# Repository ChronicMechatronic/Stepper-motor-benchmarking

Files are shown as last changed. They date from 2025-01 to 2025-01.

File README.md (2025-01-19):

# Stepper-motor-benchmarking
Collection of all test results and data from thoroughly testing my collection of random stepper motors

This repository contains all results and data from extensively testing the microstepping capabilities as well as any specifications I found online for each of the following stepper motors:

 - USONGSHINE US-17HS4401S
 - EPSON EM-257 / EM-258
 - JAPAN SERVO KP39HM2-025
 - EM-164 / STH-39D179-03 (unknown manufacturer)
 - MOONS 17HA0403-75NS
 - MOONS 16HY7401-44S
 - JAPAN SERVO KP35FM2-044
 - LIN ENGINEERING 3518M-10D-01RO
 - MERCURY MOTOR SM-42BYG011-25
 - 42HJA440-23 (unknown manufacturer)
 - TRONXY 42SHDC4080Z-25B
 - KYSAN 1124090 / 42BYGH4803-DC
 - HANPOSE 17HS4401
 - WANTAI MOTOR 42BYGHW609-1

For information about my test procedure and how to interpret the data, watch the [full video](https://www.youtube.com/watch?v=Vqqj7FCdkGw) on my YouTube channel

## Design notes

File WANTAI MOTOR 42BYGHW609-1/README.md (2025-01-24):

## WANTAI MOTOR 42BYGHW609-1 

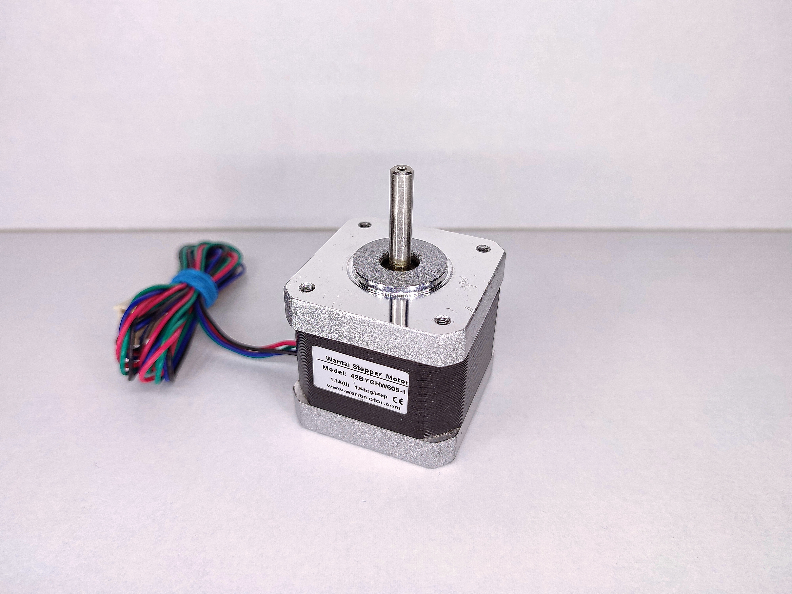
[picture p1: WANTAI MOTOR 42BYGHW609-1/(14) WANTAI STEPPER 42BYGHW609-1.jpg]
image of a stepper motor


It's a stepper motor aimed at the 3D printing industry. That's all there is to say about it. Low phase resistance, low inductance, high current - it's all pretty standard stuff. The WANTAI MOTOR website lists the specs:

 - https://www.wantmotor.com/hybrid-stepper-motor/2-phases-hybrid-stepper-motor/42byghw-stepper-motor.html
 - Open Impulse seems to have put together a datasheet for it with even a torque curve added, though at the time of writing this the site didn't manage to load for some reason: https://www.openimpulse.com/blog/wp-content/uploads/wpsc/downloadables/42BYGHW609-Stepper-Motor-Datasheet1.pdf

Good news, however, to prepare for exactly that eventuality (a site being taken down or otherwise unavailable), I added the downloaded PDFs to this repository. You're welcome!

Of course, the usual disclaimer still applies; intellectual property rights for any graphics and logos depicted in screenshots of those sites obviously go to their respective site owners and are not part of this open-source repository, as I have no rights to distribute these myself. (in other words, stating the obvious to make sure I cover my ass for legal purposes here: the fact that I'm sharing screenshots with these logos and graphics in them in a CC-BY-SA-4.0 repository doesn't mean the license extends to those graphics)

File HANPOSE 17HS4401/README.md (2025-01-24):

## HANPOSE 17HS4401

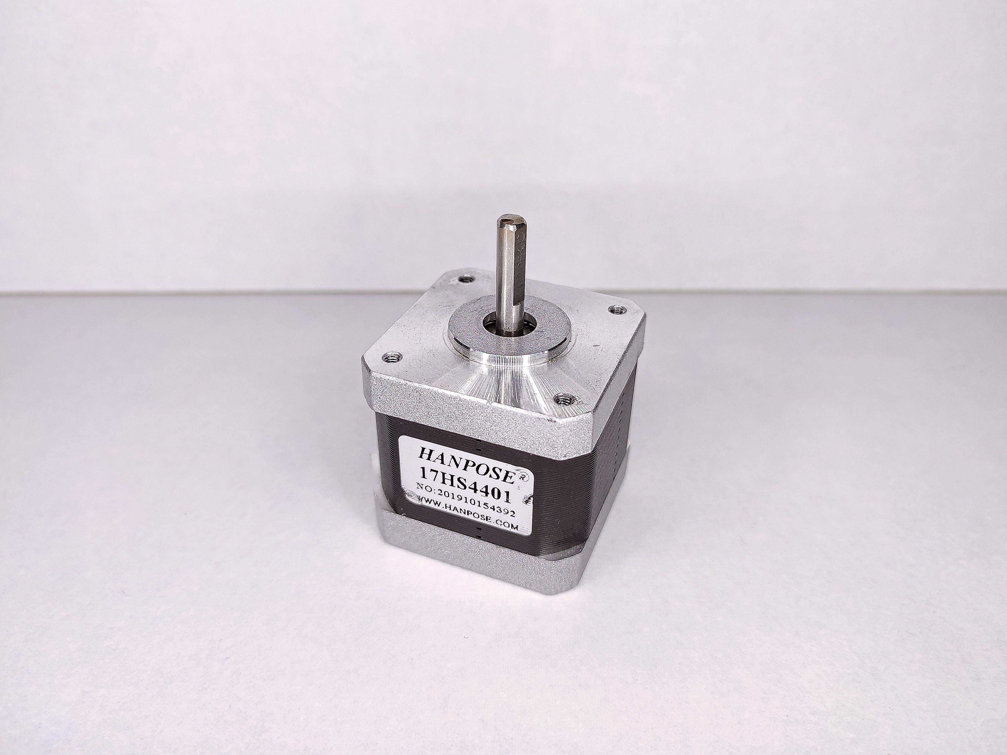
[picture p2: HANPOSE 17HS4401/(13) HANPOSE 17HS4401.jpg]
image of a stepper motor


In my opinion, companies should really stop making products with different specs under the same model number, but oh well... This is the 17HS4401 model from HANPOSE, which, compared to the USONGSHINE version, has a marginally lower holding torque at the same current - which I guess makes sense considering it also has a lower phase resistance and thereby fewer turns per coil. On the other hand, this should mean lower inductance and higher maximum speeds... I'm speculating at this point; I really wanted to see the exact differences between these two models in the dynamic torque tests, but I guess that'll have to wait for another day. In any case, there weren't any datasheets available for this motor, but the Alibaba product page lists current and holding torque at least:

 - https://www.alibaba.com/product-detail/HANPOSE-Direct-purchase-price-40N-CM_62405772411.html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

There's also an exported PDF version as a backup in case the site goes down in the future.

Intellectual property rights for any graphics and logos depicted in screenshots of websites obviously go to their respective site owners and are not part of this open-source repository.

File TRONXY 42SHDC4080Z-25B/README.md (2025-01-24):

## TRONXY 42SHDC4080Z-25B

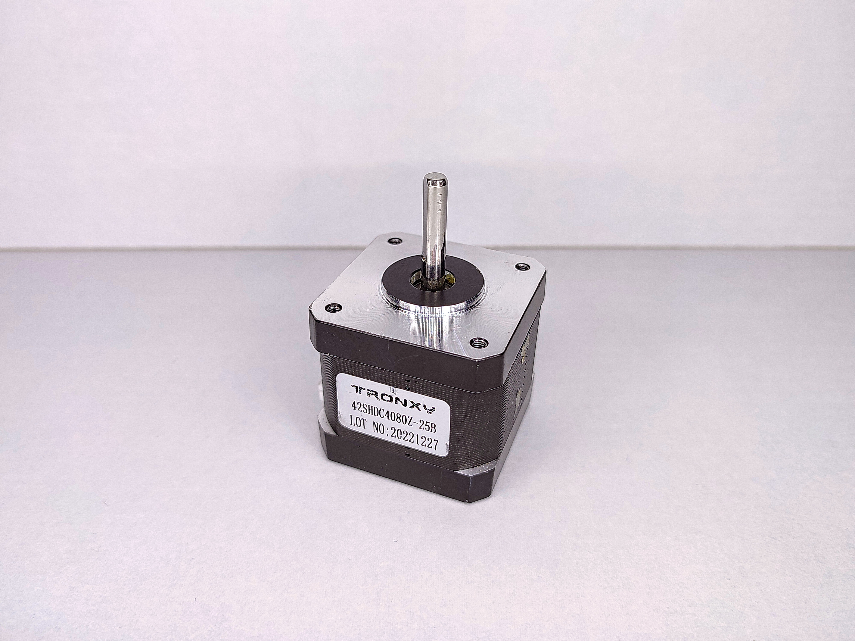
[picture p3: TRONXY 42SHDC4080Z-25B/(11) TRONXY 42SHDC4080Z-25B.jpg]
image of a stepper motor


This stepper motor is clearly from a TRONXY 3D printer, which is why I was all the more surprised by the fact that there was absolutely no info about it online. Ultimately I guess it's just another generic clone of an obscure Chinese stepper motor. Unfortunately, Tronxy also didn't bother to list any specs anywhere either, as the replacement steppers they sell on their website have a different part number altogether. They're called "SL42STH40" instead, so short of sending TRONXY an email asking about the specs (which I don't feel bold enough to do), we're basically on our own if we want specs for the 42SHDC... Or are we? With a bit of _imaginative_ reasoning, we can assume the SL42STH40 steppers they currently sell are very similar clones - after all, what are the odds they actually changed suppliers or specifications? Relatively low, is my gut feeling. Physically they look identical save for the label, which obviously doesn't say much. So since I needed a baseline current rating for my testing, I decided to just go with the same 1.8A current rating they claim for their current SL42STH motor. Though I'm honestly not sure whether to trust that rating either, despite the low 1.6Ω winding resistance suggesting this motor would indeed run at a higher current than its 3Ω NEMA 17 brethren. So in continuous use, I would probably run this motor closer to 1.5A or less, depending on how hot it gets. If you happen to have one of these, please run your own tests; even something simple with an A4988 like I did in the video will easily give you a much more reliable reference and prevent anything from being damaged. I just didn't have the time to spend another day letting stepper motors run idle in the basement.

That said, here are the few most relevant-looking search results I was able to come up with:

 - https://www.tronxy3d.com/collections/motor/products/sl42sth40-1684a-1-8a-78oz-in-42-stepper-motor
 - https://botland.store/flashforge-replacement-parts/18649-stepper-motor-42shdc1065z-19wt-200-steps-448v-08a-028nm-for-flashforge-adventurer-3-5904422362294.html
 - https://www.tronxy3d.com/products/tronxy-3d-printer-parts-sl42sth60-1684a-motor-with-1-5m-cable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
 - https://www.alibaba.com/product-detail/42SHDC3025-24B-stepper-motor-for-eco_1600961608090.html
 - https://french.alibaba.com/product-detail/CE-Approved-2-Phase-Stepper-1-62149025114.html

There are also exported PDF versions for some of these sites as a backup in case any of them goes down in the future.

Intellectual property rights for any graphics and logos depicted in screenshots of those sites obviously go to their respective site owners and are not part of this open-source repository, as I have no rights to distribute these myself. (in other words, stating the obvious to make sure I cover my ass for legal purposes here: the fact that I'm sharing screenshots with these logos and graphics in them in a CC-BY-SA-4.0 repository doesn't mean the license extends to those graphics)

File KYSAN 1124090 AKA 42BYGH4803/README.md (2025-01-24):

## KYSAN 1124090 / 42BYGH4803

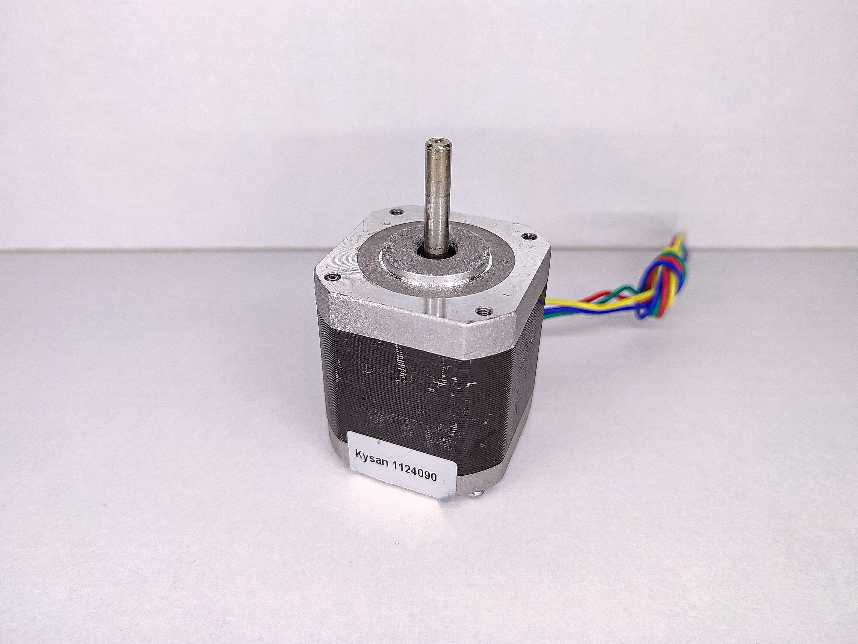
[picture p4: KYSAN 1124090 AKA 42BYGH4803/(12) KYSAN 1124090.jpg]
image of a stepper motor


Apparently this 42BYGH4803 stepper motor was rather common in RepRap 3D printers back in the day. It's from KYSAN with the SKU 1124090, and I really can't think of anything else to say about it. It's a stepper motor, I guess.

Here are the relevant links to product pages listing the specs and datasheets:

 - https://kysanelectronics-com.3dcartstores.com/42BYGH4803-DC_p_672.html
 - https://www.kysanelectronics.com/graphics/1124090-8.3.15.pdf
 - https://ultimachine.com/products/kysan-1124090-nema-17-stepper-motor
 - https://cdn.shopify.com/s/files/1/1223/5992/files/1124090_Torque_curve_diagram.pdf?6848101445132525963
 - https://cdn.shopify.com/s/files/1/1223/5992/files/Nema17StepperMotor.pdf?6848101445132525963

There are also PDF versions of the datasheets as a backup in case any of the websites go down in the future.

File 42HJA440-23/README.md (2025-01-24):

## 42HJA440-23 (unknown manufacturer)

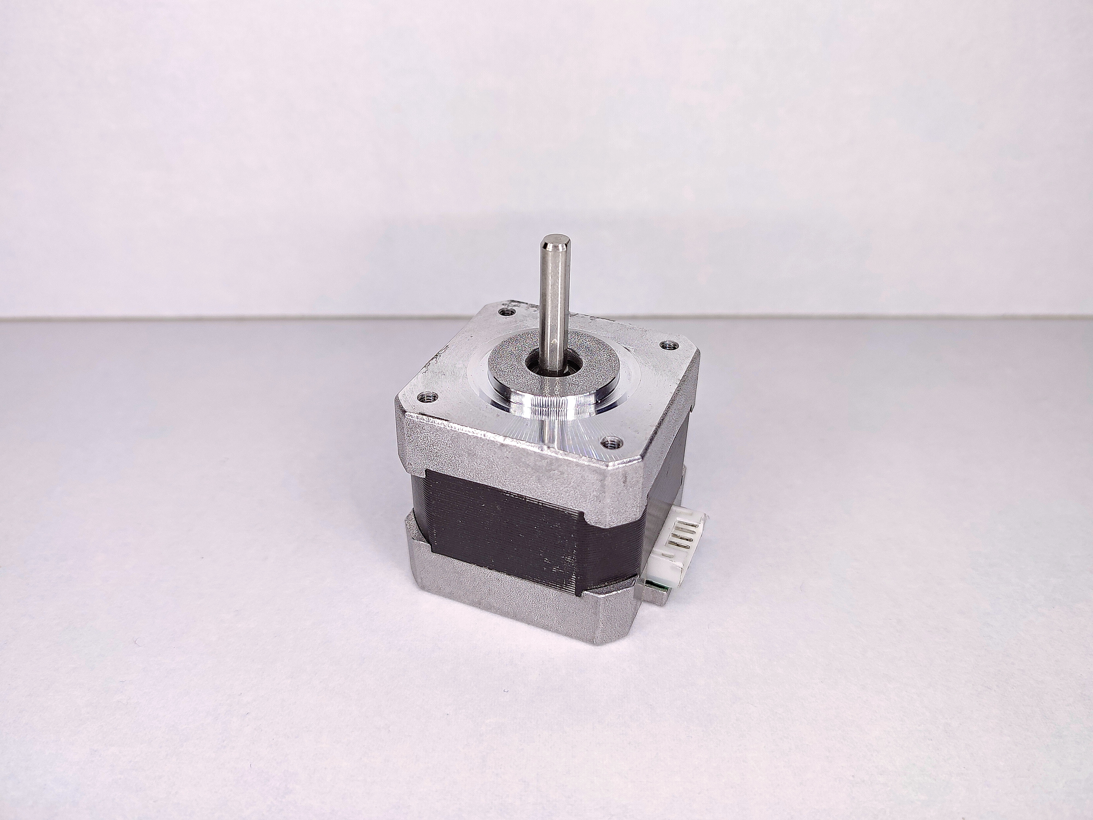
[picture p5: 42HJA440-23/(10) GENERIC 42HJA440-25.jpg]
image of a stepper motor


This stepper motor is a total mystery - it looks about as generic as things can get, and the total lack of identifying features other than the part number stamped on the back makes it all the more intriguing to me. But probably it's just another clone of a clone. I'll certainly work fine for a 3D printer or something, with a microstepping performance on par with that of most other modern Chinese low-cost steppers. Since I didn't find a concrete current rating, I theoretically should've established a new one through actual testing, but seeing as these NEMA 17s are all so similar, I basically just guesstimated a value that felt right. Taking the relatively low phase resistance of only 1.5Ω into account, I went with 1.64A, which is definitely as arbitrary as it is to be taken with a grain of salt. In continuous use, I would probably run this motor closer to 1.5A or less, depending on how hot it gets. If you happen to have one of these, please run your own tests; even something simple with an A4988 like I did in the video will easily give you a much more reliable reference and prevent anything from being damaged. That said, I needed a baseline for my testing and couldn't spend another day letting stepper motors run idle in the basement.

Here some of the search results that sounded the most relevant, though none of them is actually referring to this model as far as I can tell:

 - https://www.made-in-china.com/showroom/seaweedtan/product-detailzMAEstGCaZRr/China-42mm-Stepper-Motor-for-Lighting-Equipment-42HJA440-20-.html
 - https://www.ubuy.fr/en/catalog/product/view/id/12983460/s/dp-cinkco-nema-17-stepper-motor-2phase-17-bipolar
 - https://www.machineto.com/textile-printing-equipment-stepper-motor-10238961

There are also exported PDF versions for each of these sites as a backup in case any of them goes down in the future.

Intellectual property rights for any graphics and logos depicted in screenshots of those sites obviously go to their respective site owners and are not part of this open-source repository, as I have no rights to distribute these myself. (in other words, stating the obvious to make sure I cover my ass for legal purposes here: the fact that I'm sharing screenshots with these logos and graphics in them in a CC-BY-SA-4.0 repository doesn't mean the license extends to those graphics)

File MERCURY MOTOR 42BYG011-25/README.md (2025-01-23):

## MERCURY MOTOR 42BYG011-25

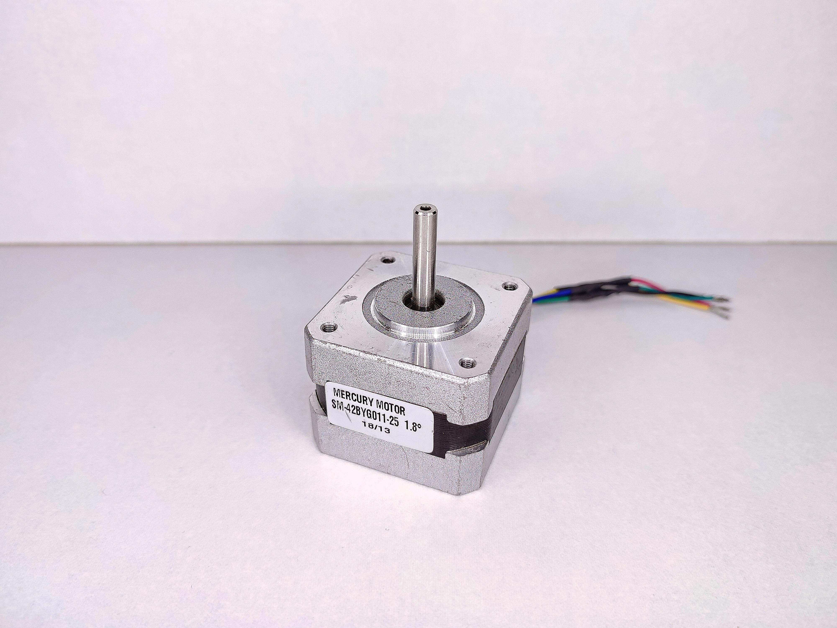
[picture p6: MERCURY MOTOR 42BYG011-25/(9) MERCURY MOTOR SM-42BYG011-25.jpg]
image of a stepper motor


This stepper is from Sparkfun and readily available on DigiKey - it also has a very high phase resistance of 34 ohms, which is definitely unusual. I don't know why bipolar motors with this winding configuration are even still manufactured, seeing as the general push has been towards low-resistance, actively current-controlled motors for years now, but I guess there are a few niche applications where having the current regulated passively by good old Ohm's law prevails over modern alternatives by enabling a simple H-bridge drive circuitry to be used.

 - Here the product page on DigiKey: https://www.digikey.com/en/products/detail/sparkfun-electronics/ROB-09238/5318747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
 - And the datasheet, of course: https://www.sparkfun.com/datasheets/Robotics/SM-42BYG011-25.pdf

There are also exported PDF versions for each of these sites as a backup in case any of them goes down in the future.

Intellectual property rights for any graphics and logos depicted in screenshots of those sites obviously go to their respective site owners and are not part of this open-source repository, as I have no rights to distribute these myself. (in other words, stating the obvious to make sure I cover my ass for legal purposes here: the fact that I'm sharing screenshots with these logos and graphics in them in a CC-BY-SA-4.0 repository doesn't mean the license extends to those graphics)

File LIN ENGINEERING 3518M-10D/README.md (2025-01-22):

## LIN ENGINEERING 3518M-10D

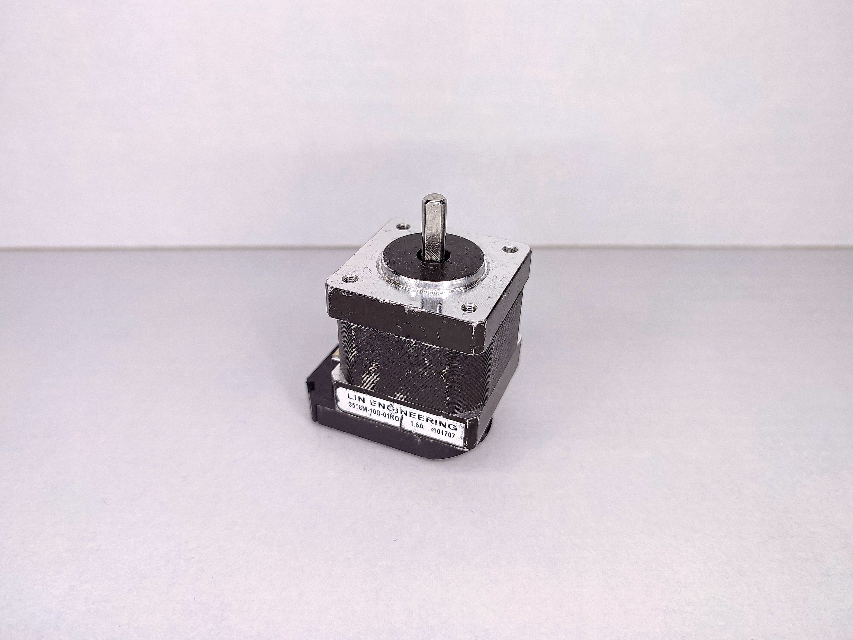
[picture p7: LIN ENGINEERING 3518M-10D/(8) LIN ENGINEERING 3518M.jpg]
image of a stepper motor


While LIN ENGINEERING (being a subsidiary of MOONS) generally provides good documentation for their stepper motors, this one sure seems like a customized version of one of their models - the coil parameters of this one don't match up at all with the ones they list on their website for the 3518M - it has a phase resistance of only about 1.0 ohm, which doesn't fit in with any of their other model series either as far as I could tell. Fortunately, the current rating is printed right on the label, so the lack of other specifications didn't impede my testing.

 - Here's a link to their 3518M series, though I wouldn't rely on any of the electrical specifications: https://www.linengineering.com/products/stepper-motors/hybrid-stepper-motors/3518-series/3518M-07

 - And another NEMA 14 of theirs with a similar current rating that I at first thought they might've taken the coil configuration from, but it still has twice the phase resistance of mine... https://www.linengineering.com/products/stepper-motors/hybrid-stepper-motors/3518-series/3518L-15P

There are also exported PDF versions of these sites as a backup in case any of them goes down in the future.

Intellectual property rights for any graphics and logos depicted in screenshots of those sites obviously go to their respective site owners and are not part of this open-source repository, as I have no rights to distribute these myself. (in other words, stating the obvious to make sure I cover my ass for legal purposes here: the fact that I'm sharing screenshots with these logos and graphics in them in a CC-BY-SA-4.0 repository doesn't mean the license extends to those graphics)

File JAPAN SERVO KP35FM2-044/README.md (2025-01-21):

## JAPAN SERVO KP35FM2-044

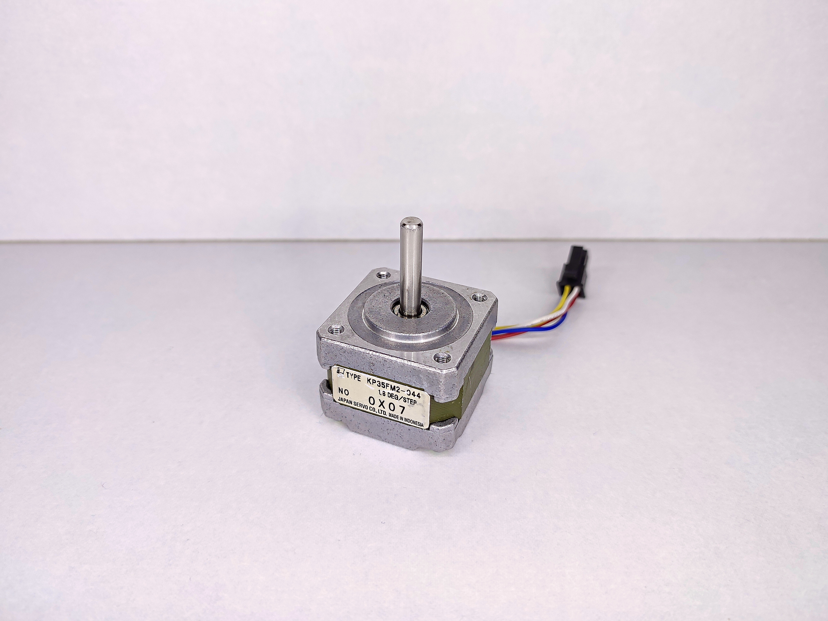
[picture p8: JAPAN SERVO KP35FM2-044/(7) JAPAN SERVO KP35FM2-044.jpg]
image of a stepper motor


Another stepper motor from JAPAN SERVO - though this one is fortunately bipolar and quite usable in its stock configuration. I was actually able to find two references to this exact model online.

 - A product page for it on some (Serbian?) website: https://www.interhit.rs/razno/12919-mot-kp35fm2-044-2000000137841.html
 - A page of some mail-order-catalog listing the important specs: https://www.jameco.com/Jameco/catalogs/c111/P113.pdf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

No real datasheets, though unfortunately. I also included exported PDF versions for each of these sites as a backup in case any of them goes down in the future.

Intellectual property rights for any graphics and logos depicted in screenshots of those sites obviously go to their respective site owners and are not part of this open-source repository, as I have no rights to distribute these myself. (in other words, stating the obvious to make sure I cover my ass for legal purposes here: the fact that I'm sharing screenshots with these logos and graphics in them in a CC-BY-SA-4.0 repository doesn't mean the license extends to those graphics)

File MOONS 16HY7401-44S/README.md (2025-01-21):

## MOONS 16HY7401-44S

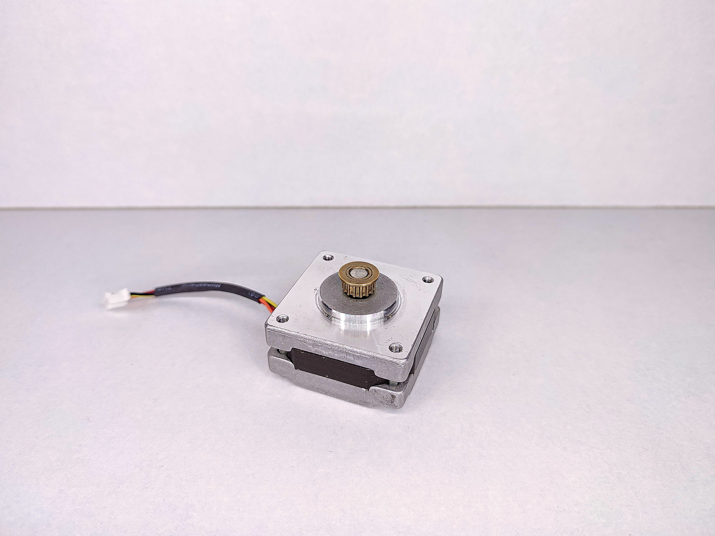
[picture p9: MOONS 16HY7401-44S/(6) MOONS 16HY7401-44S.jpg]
image of a stepper motor


Yet another pancake stepper from MOONS with an annoying brass pulley on it - finding even a picture of a matching unit was impossible, but I managed to find some specs on an ancient derelict website:

 - http://www.huaning.com/oldwebsite/electrical/16hy.htm

Not sure if this is specifically for the MOONS edition of this motor or maybe some other manufacturer's version of it (since I noticed, just like with semiconductors, the more popular models seem to be made by several different companies with very slightly different specs), though seeing as I wasn't able to find anything else whatsoever, it's safe to assume these are the right specs for the stepper.

There's also an exported PDF version of this site as a backup in case somebody remembers to decommission that forgotten-about server in the corner and takes the site down in the future.

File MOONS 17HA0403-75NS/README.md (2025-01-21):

## MOONS 17HA0403-75NS

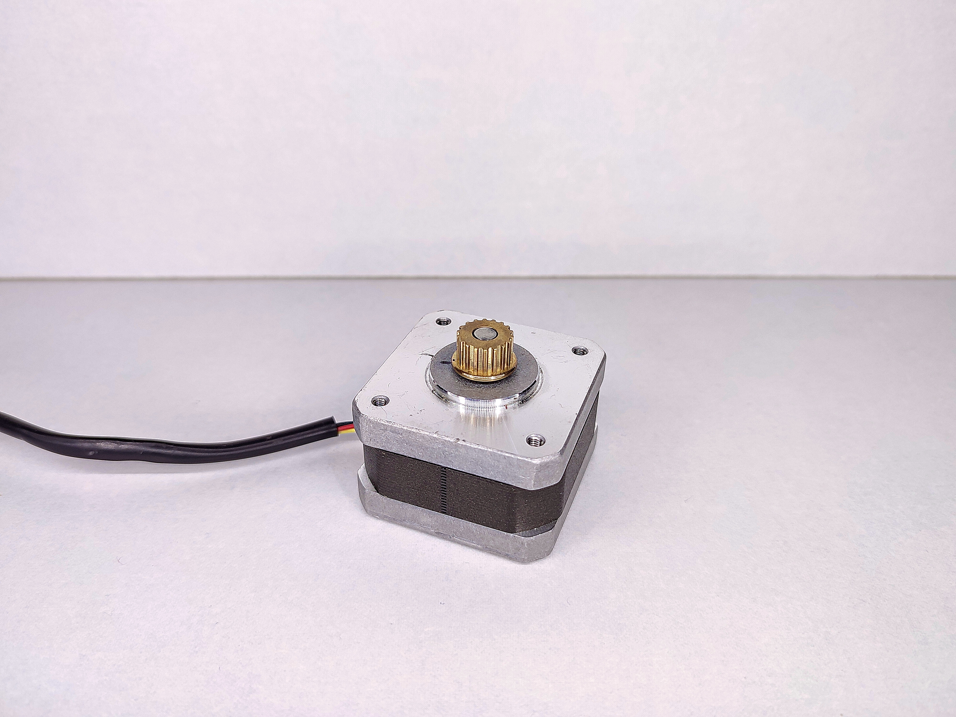
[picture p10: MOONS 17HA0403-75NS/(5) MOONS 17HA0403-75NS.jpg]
image of a stepper motor


I really can't say what device this stepper motor is from - the brass pulley on it is not GT2 size though, so for most DIY projects you'll probably have to remove it, which is more than a little annoying. I recommend a hacksaw to destroy the pulley as the easiest way to get it off - I wanted to keep the motor and the pulley intact, so I had to machine a custom gear puller that actually fit in the tight gap between the motor housing and the pulley flange.

Fortunately, I was able to find what I am relatively confident is the datasheet for this motor - there's even two versions of it:

- https://datasheet4u.com/datasheet-pdf/ETC/17HA0403-44N/pdf.php?id=977470
- http://www.motionusa.com.s3-website-us-east-1.amazonaws.com/moons/Hybrid_Stepper_Motors_17HA_Series.pdf

There's also a very similar looking one with a 1.8 step angle instead, though I think it might not be from MOONS - No idea what you might need this for, but here's the link anyway:
 - https://www.sinoning.com/product/17ha0403-17n-micro-precision-stepper-motor-42mm-1-8-degree-2-phase-4-wire-stepping-motor-pulley-cnc-3d-printer-diy/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

There are also exported PDF versions for each of these sites as a backup in case any of them goes down in the future.

Intellectual property rights for any graphics and logos depicted in screenshots of those sites obviously go to their respective site owners and are not part of this open-source repository, as I have no rights to distribute these myself. (in other words, stating the obvious to make sure I cover my ass for legal purposes here: the fact that I'm sharing screenshots with these logos and graphics in them in a CC-BY-SA-4.0 repository doesn't mean the license extends to those graphics)

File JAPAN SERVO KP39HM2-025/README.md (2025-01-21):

## JAPAN SERVO KP39HM2-025

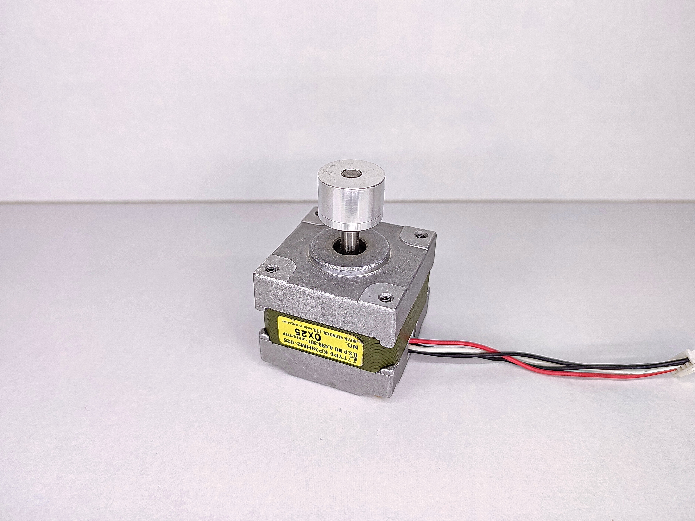
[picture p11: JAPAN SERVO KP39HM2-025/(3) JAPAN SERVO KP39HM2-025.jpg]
image of a stepper motor


This motor is difficult. Apparently, it came from a 5 1/4-inch disk drive, so it must be quite old at this point - which explains why it was actually unipolar in its stock configuration. I disassembled mine and wired both sides of the center tap in each coil in parallel to reduce total phase resistance and inductance for use in a bipolar configuration. It's not quite the usual unipolar-to-bipolar mod, so here's an image for illustration:
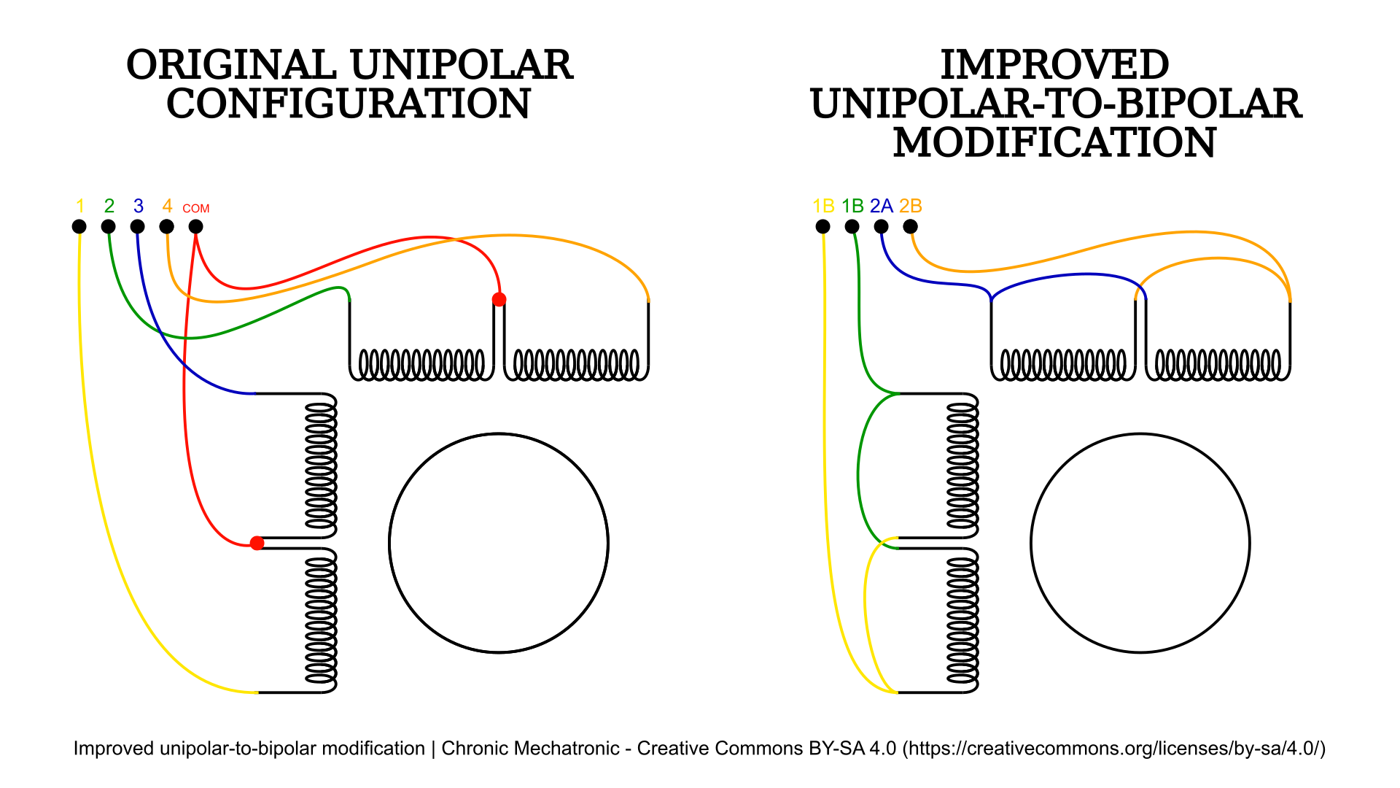
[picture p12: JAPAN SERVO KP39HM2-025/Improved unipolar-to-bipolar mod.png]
improved unipolar-to-bipolar wiring configuration


Given that I ran my tests after doing these modifications to the motor, all the data you see here will obviously only apply to models of this stepper that underwent the same treatment (which I don't recommend doing, btw, as it turned out the air gap between the rotor and stator is only like 0.1mm all around, which means it's basically impossible to reassemble the motor without the rotor scraping against the stator laminations unless you have some very specific alignment tools at your disposal. That's something I didn't mention in the video.)

Through trial & error I determined an appropriate operating current for my modified motor to be 0.23A, which is surprisingly close to the 0.2A I saw specified on some websites I found.
Here are links to everything I found online about this motor:

 - Forum post from 2003 mentioning the 5 1/4-inch disk drive: https://forum.nutsvolts.com/viewtopic.php?t=4466
 - The broken product page listing voltage and current: http://us.100y.com.tw/PNoInfo/9743.htm
 - Another product page confirming that info: https://www.yoycart.com/Product/544148608932/

There are also exported PDF versions for each of these sites as a backup in case any of them goes down in the future.

Intellectual property rights for any graphics and logos depicted in screenshots of those sites obviously go to their respective site owners and are not part of this open-source repository, as I have no rights to distribute these myself. (in other words, stating the obvious to make sure I cover my ass for legal purposes here: the fact that I'm sharing screenshots with these logos and graphics in them in a CC-BY-SA-4.0 repository doesn't mean the license extends to those graphics)

I originally planned to use this motor in a 3D printer, so I made a pretty detailed CAD model for it. I included the .STEP file here, but you can also download it from my GrabCAD:
 - https://grabcad.com/library/nema-16-stepper-motor-kp39hm2-025-1

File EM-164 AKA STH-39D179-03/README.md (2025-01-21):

## EM-164 / STH-39D179-03

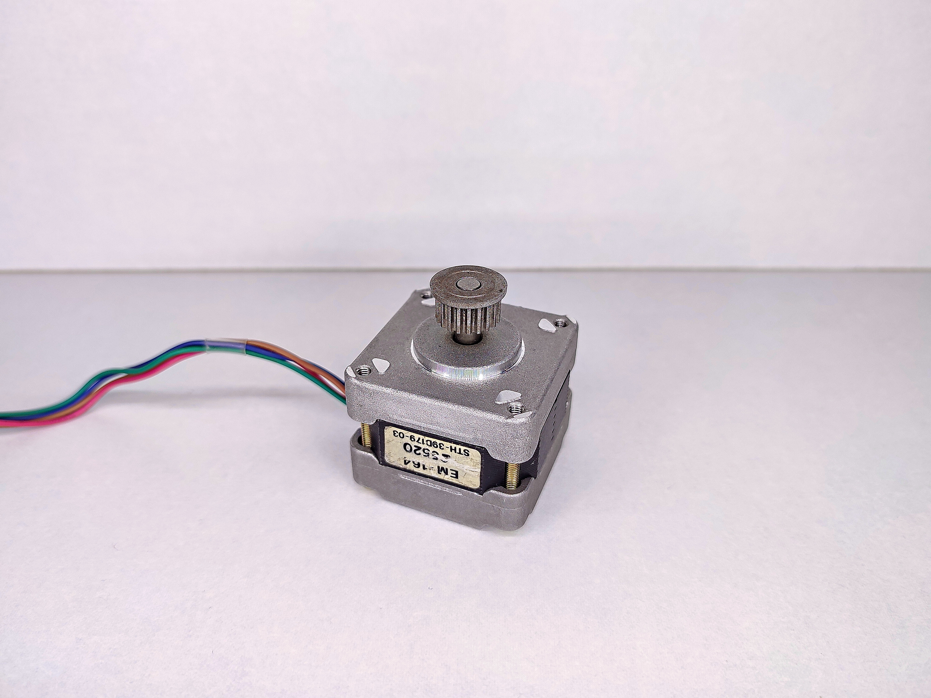
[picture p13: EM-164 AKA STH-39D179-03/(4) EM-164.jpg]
image of a stepper motor


The provenance of this stepper is a mystery - as is pretty much the entire motor. I found no reference whatsoever to this stepper motor, not even an image of an exact match, which is kind of surprising. What I do know is that it used to be unipolar - I disassembled mine and wired both sides of the center tap in each coil in parallel to reduce total phase resistance and inductance for use in a bipolar configuration. It's not quite the usual unipolar-to-bipolar mod, so here's an image for illustration:
improved unipolar-to-bipolar wiring configuration

Prior to this modification, the phase resistance used to be about 5.8Ω, which was halved to around 2.9Ω, a fairly common value for bipolar stepper motors. 
Seeing as this would've rendered all existing electrical specifications irrelevant anyway, the fact that I didn't find anything about this motor online wasn't a big problem - I simply determined a new appropriate operating current via trial and error. The current at which the stepper heated up to no more than 70°C at a room temperature of 20°C was 0.74 Amperes. The 70°C temperature limit was picked rather arbitrarily; the actual maximum operating temperature would be more like 80°C, as that's where the neodymium magnets start to degrade, so 70°C leaves some room for error. 

Given that I ran my tests after doing these modifications to the motor, all the data you see here will obviously only apply to models of this stepper that underwent the same treatment (which I don't recommend doing, btw, as it turned out the air gap between the rotor and stator is only like 0.1mm all around, which means it's basically impossible to reassemble the motor without the rotor scraping against the stator laminations unless you have some very specific alignment tools at your disposal. That wasn't an issue for me with this specific motor, but I'll mention it here anyway since it was a problem for the other motors I took apart)

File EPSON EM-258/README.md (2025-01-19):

## EPSON EM-257 / EM-258

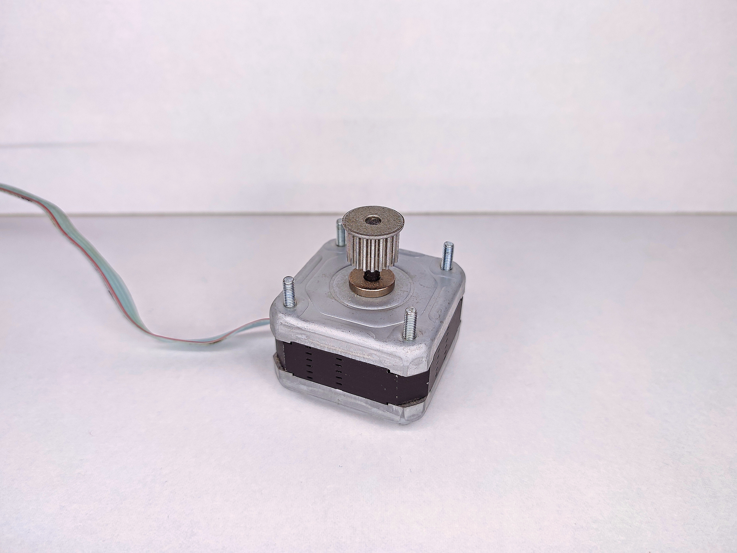
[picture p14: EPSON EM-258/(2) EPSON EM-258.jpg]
image of a stepper motor


These apparently come as a pair in the old Epson Stylus inkjet printers. I was never lucky enough to disassemble one of these printers myself, but based on the gears and pulleys that were on the shaft when I got the motors, I'd think the EM-257 was driving the print head while the EM-258 was for the paper feed. Good times when even inkjet printers had NEMA 17s inside...
That said, despite the slightly different naming and physical appearance, from what I could see, both these steppers were customized versions of the same motor called 17PM-K212-PIT from Astrosyn at the time, so I simply lumped them together for testing.

There is some ambiguity about the rated current for this motor since the closest thing I found to a datasheet for the 17PM-K212-PIT mentioned 0.6A phase curent but the old website entry for the EM-258 stated 0.7A, which is what I ultimately went with.

That being said, here are links to everything I found about them on the web:

 - The random Google spreadsheet listing which printers these motors can be salvaged from: https://docs.google.com/spreadsheets/d/1TOAJp6hJdnVPc86Z5KwxvSGqu_2xwKQJDcFqrtlP1YU/htmlembed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
 - The (extremely slow) old website stating the specs: http://www.motors.wrobots.com/EM-258_17PM-K212-PIT.php
 - And a sort of "datasheet" for the 17PM-K212-PIT: https://www.roboternetz.de/phpBB2/files/17pm-k212-p1t.pdf

There are also exported PDF versions for each of these sites as a backup in case any of them goes down in the future.

Intellectual property rights for any graphics and logos depicted in screenshots of those sites obviously go to their respective site owners and are not part of this open-source repository, as I have no rights to distribute these myself. (in other words, stating the obvious to make sure I cover my ass for legal purposes here: the fact that I'm sharing screenshots with these logos and graphics in them in a CC-BY-SA-4.0 repository doesn't mean the license extends to those graphics)

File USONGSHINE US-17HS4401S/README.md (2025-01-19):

## USONGSHINE US-17HS4401S

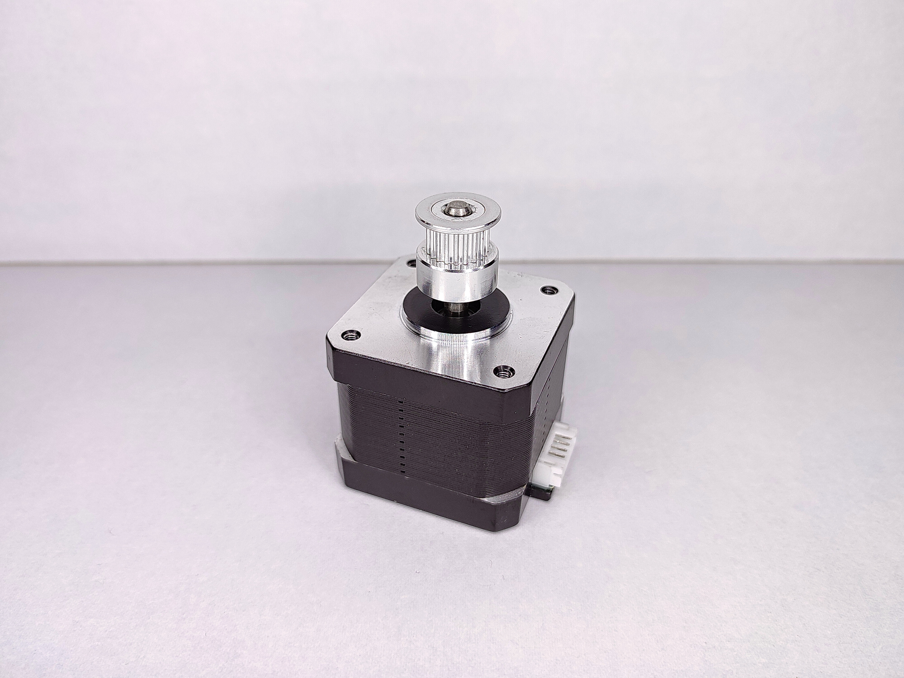
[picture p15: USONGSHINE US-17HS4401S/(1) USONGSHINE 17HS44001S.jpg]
image of a stepper motor


This is the Usongshine-branded version of the seemingly fairly popular 17HS4401. It's set apart from some of its competitors by the slightly lower rated current of 1.5A and higher phase resistance. 
To my knowledge, the only difference between the 17HS4401 and the 17HS4401S version is the painted black endcaps as opposed to the usual cast aluminum look.

There was no official datasheet to be found for this stepper motor; the only specifications I was able to find were on the Aliexpress product page, so I'll include the link for it here:
https://www.aliexpress.us/item/3256803184327483.html?gatewayAdapt=glo2usa4itemAdapt

There's also an exported PDF of the site in case it gets taken down in the future, as well as a detailed CAD model I drew of this motor on thingiverse: https://www.thingiverse.com/thing:6761583

Intellectual property rights for any graphics and logos depicted in screenshots of those sites obviously go to their respective site owners and are not part of this open-source repository, as I have no rights to distribute these myself.
(in other words, stating the obvious to make sure I cover my ass for legal purposes here: the fact that I'm sharing screenshots with these logos and graphics in them in a CC-BY-SA-4.0 repository doesn't mean the license extends to those graphics)

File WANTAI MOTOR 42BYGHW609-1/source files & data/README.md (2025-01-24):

The pictures starting with "IMG_20241223_[...]" are the completely unedited raw photos as I pulled them from the camera.

The ones named just "WANTAI STEPPER 42BYGHW609" followed by the drive voltage/current are straightened, cropped, and otherwise edited to make them more presentable.

"comparison sheet.svg" and "microstepping chart.odt" are the Inkscape and LibreOffice source documents I put the final microstepping data sheet together in, just in case you need to make some changes (cause, well, I said it was open source)

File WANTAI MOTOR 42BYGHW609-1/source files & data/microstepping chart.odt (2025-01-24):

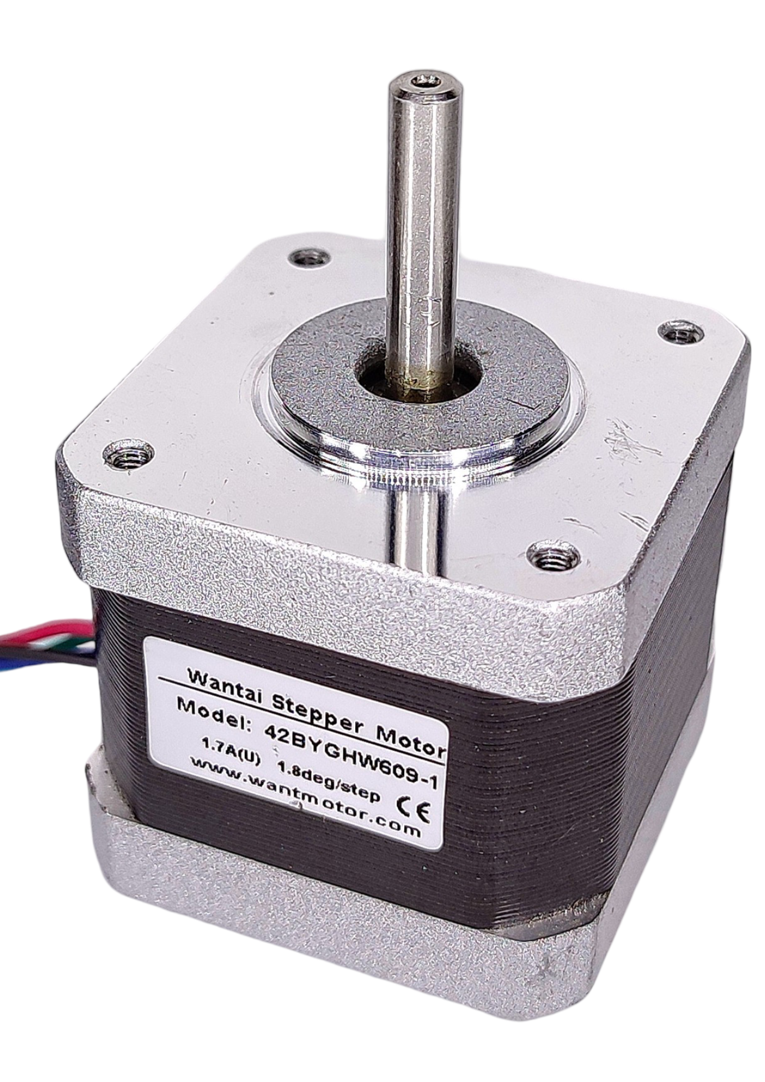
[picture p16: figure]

Microstepping Chart

Frame Size: NEMA 17

Rated Current: DC 1.7A/Phase

Holding Torque: 0.4N·m

Step Angle (degrees): 1.8°

Phase Resistance: ~2.0Ω/Phase

Test Conditions:

◾ A4988 driver used for all tests

◾ Tested at 25%, 50%, 75%, and 100% of the rated current

◾ Tested with a driver supply voltage of 12V and 24V

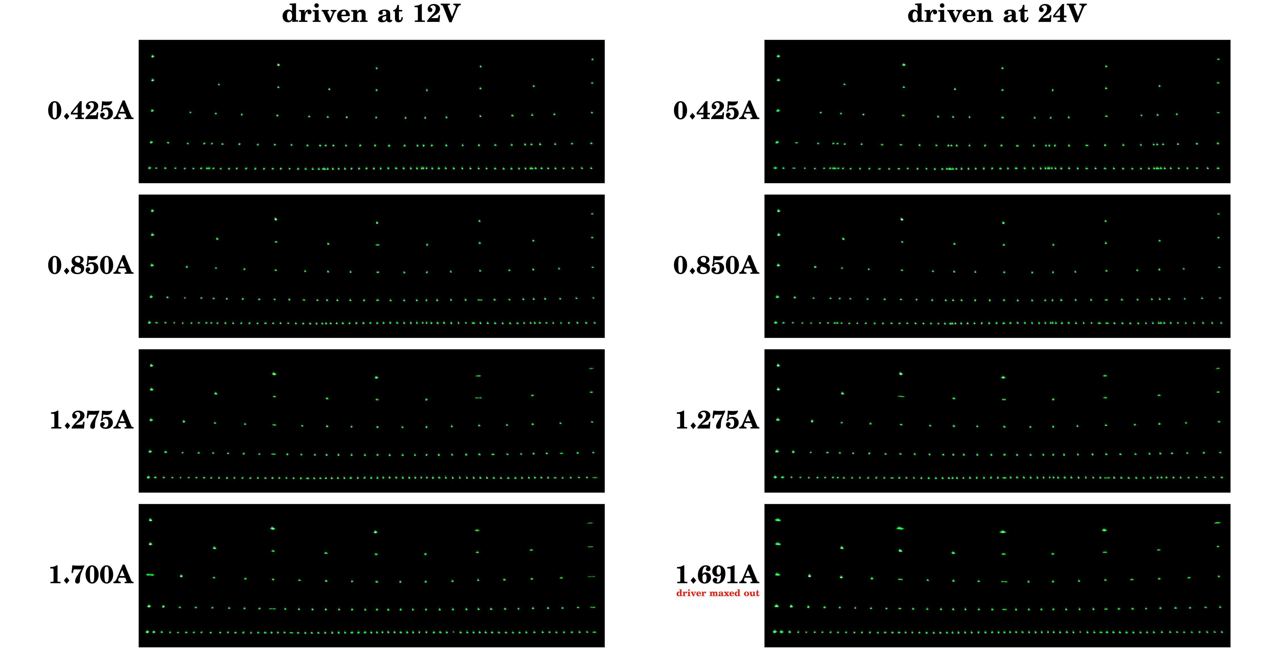
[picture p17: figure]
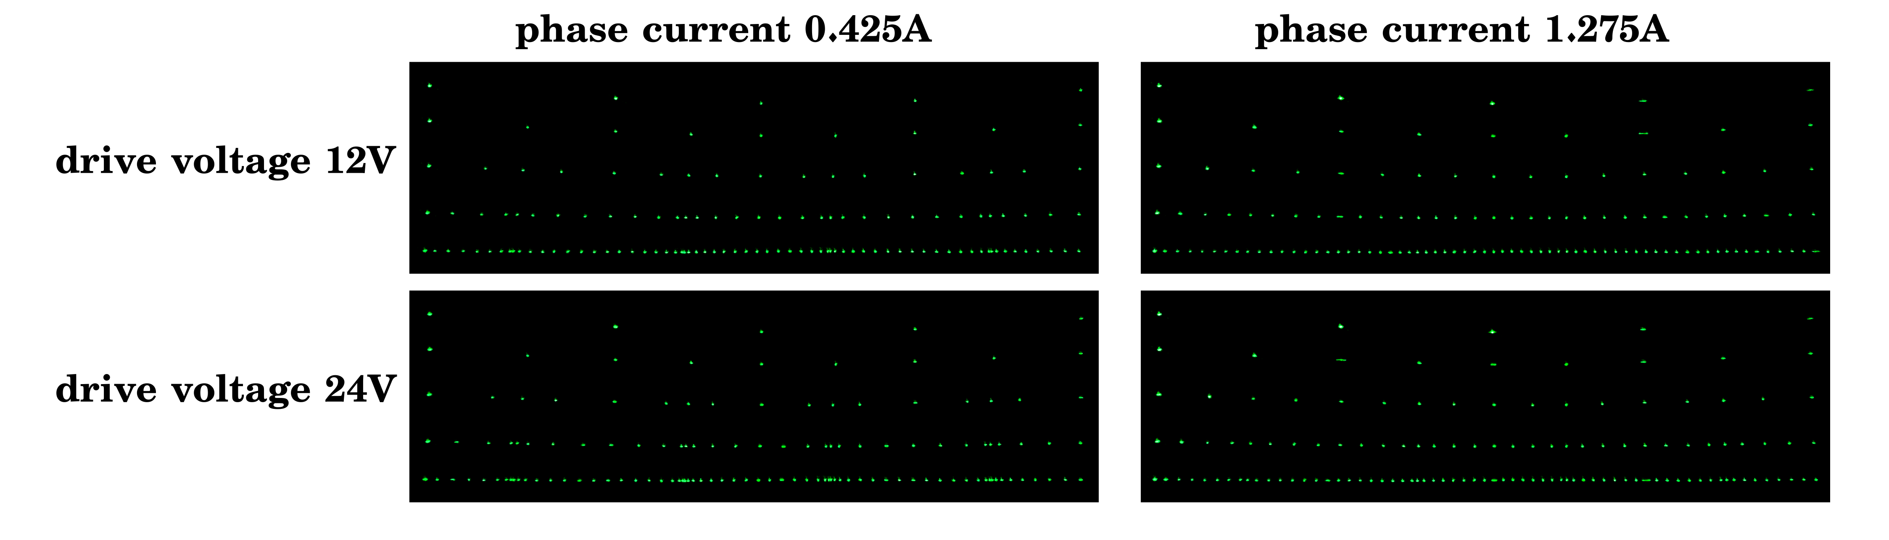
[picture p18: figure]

Notes:

◾ Every pattern was created at the indicated voltage and current levels by a laser galvo projector with the X-mirror actuated by the test subject. In automated fashion, a line of dots was drawn with the driver set to full steps, then the same row in half steps lined up underneath, then quarter steps, etc., all the way down to sixteenth steps.

◾ Due to the limited exposure duration of my camera, some combinations of drive current and voltage resulted in motion blur from the mirror ‘bouncing’ more than usual before settling at its intended target position. Other than in extreme cases, this should not significantly impact data accuracy.

WANTAI MOTOR 42BYGHW609

Chronic Mechatronic stepper motor benchmark – Creative Commons BY-SA 4.0 (https://creativecommons.org/licenses/by-sa/4.0/)

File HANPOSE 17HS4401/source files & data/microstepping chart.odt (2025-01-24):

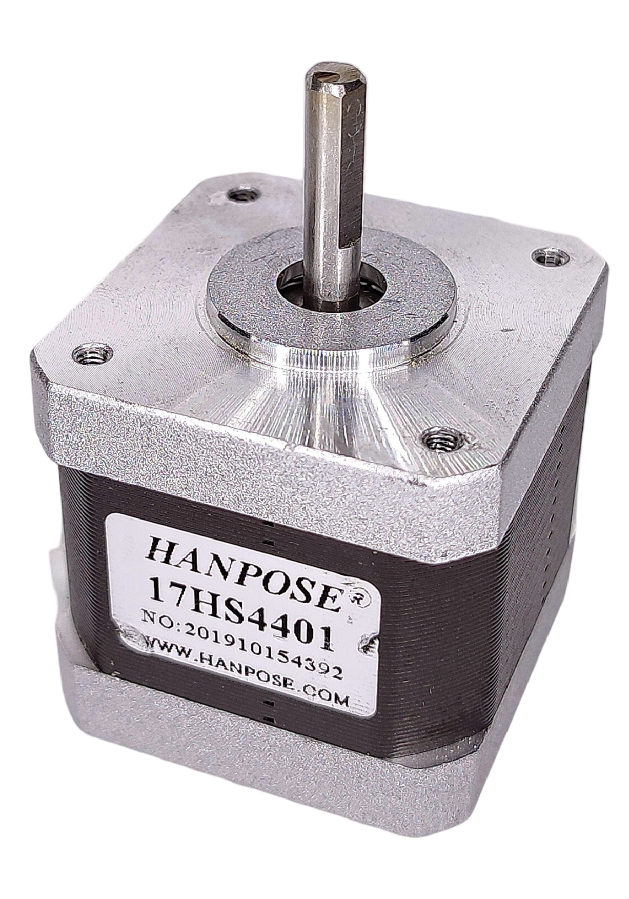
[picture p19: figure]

Microstepping Chart

Frame Size: NEMA 17

Rated Current: DC 1.5A/Phase

Holding Torque: 0.4N·m

Step Angle (degrees): 1.8°

Phase Resistance: ~1.8Ω/Phase

Test Conditions:

◾ A4988 driver used for all tests

◾ Tested at 25%, 50%, 75%, and 100% of the rated current

◾ Tested with a driver supply voltage of 12V and 24V

*(some of the higher-voltage, higher-current data points were corrupted due to driver overload)

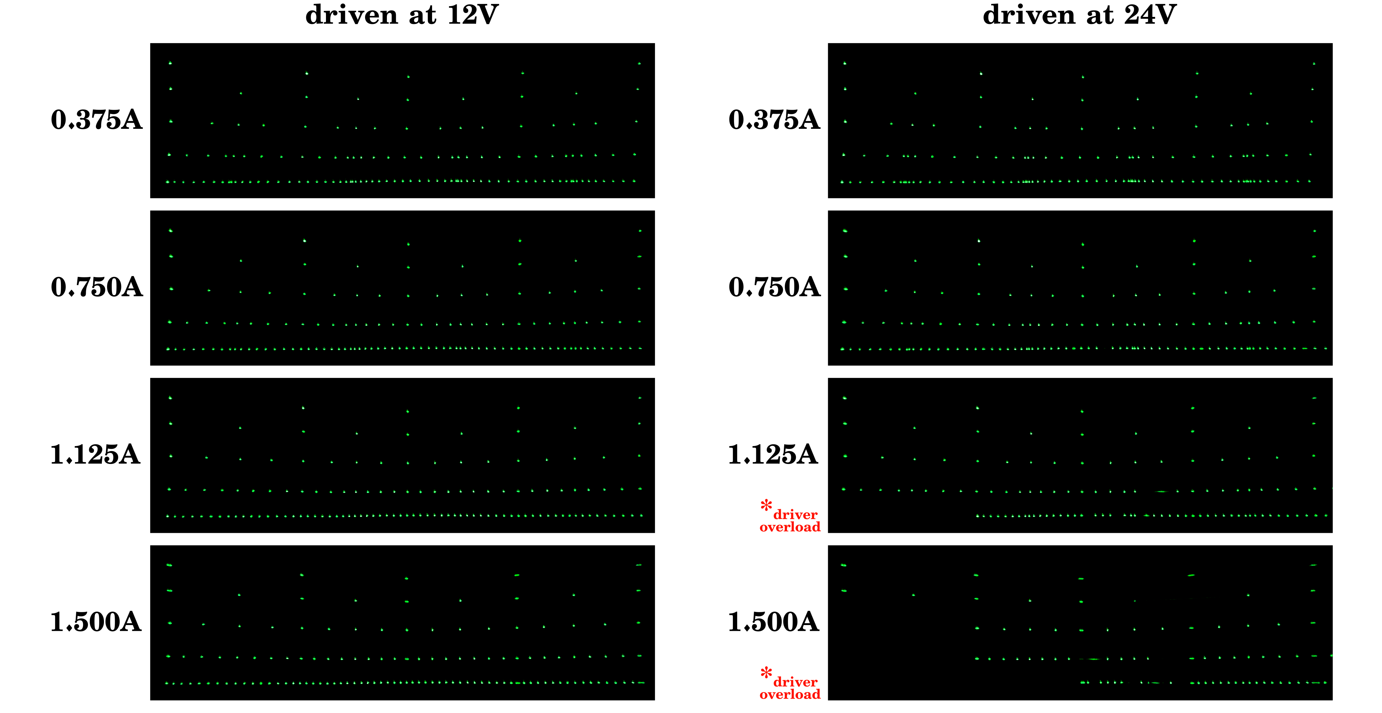
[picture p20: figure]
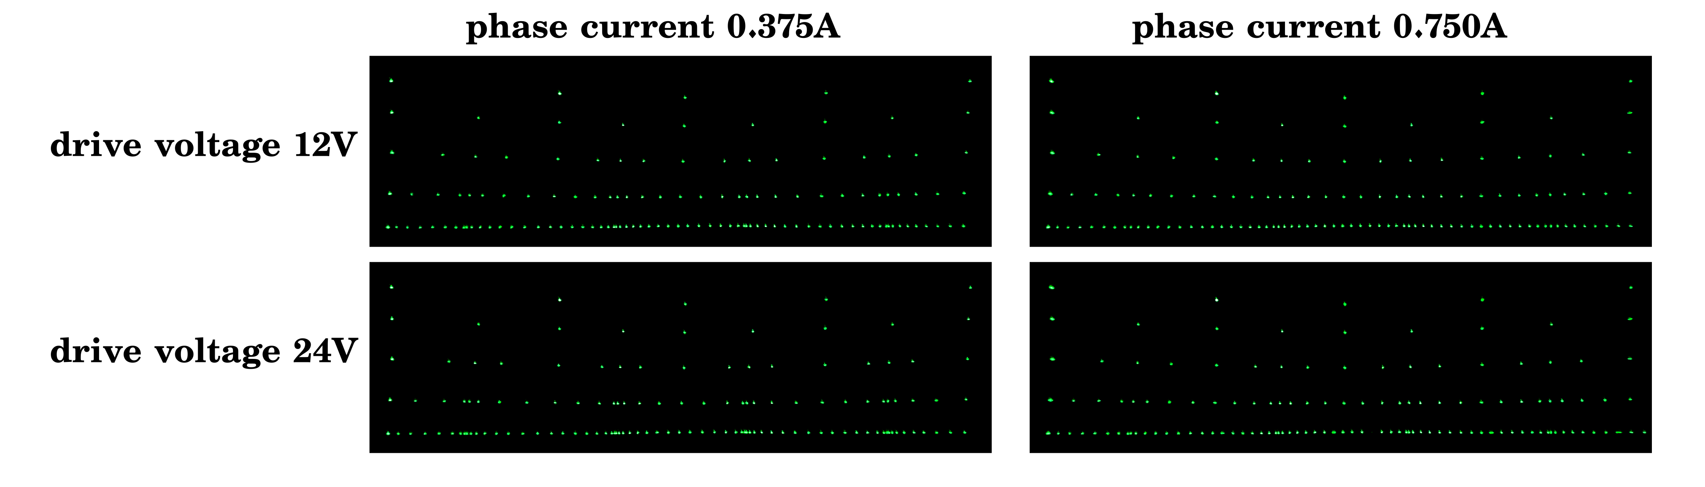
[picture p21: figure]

Notes:

◾ Every pattern was created at the indicated voltage and current levels by a laser galvo projector with the X-mirror actuated by the test subject. In automated fashion, a line of dots was drawn with the driver set to full steps, then the same row in half steps lined up underneath, then quarter steps, etc., all the way down to sixteenth steps.

◾ Due to the limited exposure duration of my camera, some combinations of drive current and voltage resulted in motion blur from the mirror ‘bouncing’ more than usual before settling at its intended target position. Other than in extreme cases, this should not significantly impact data accuracy.

◾ At ‘high’ voltages and currents of 24 volts and more than 1 ampere, the A4988 driver quickly overheats, which seems to make it extremely susceptible to electrical noise and glitching and unfortunately resulted in erratic behavior like lost steps, making execution of a complete test pattern impossible. Step detent points should still be valid wherever they visually appear in the correct location though.

Chronic Mechatronic stepper motor benchmark – Creative Commons BY-SA 4.0 (https://creativecommons.org/licenses/by-sa/4.0/)

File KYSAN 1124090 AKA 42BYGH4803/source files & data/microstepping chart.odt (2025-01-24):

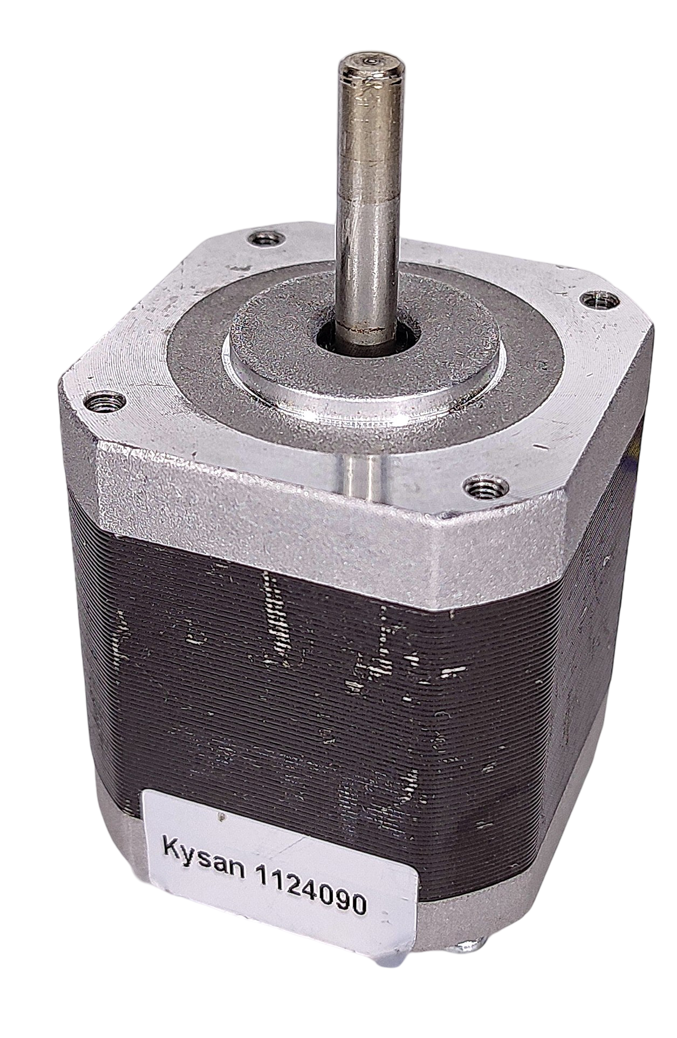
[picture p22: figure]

Microstepping Chart

Frame Size: NEMA 17

Rated Current: DC 1.5A/Phase

Holding Torque: 0.54N·m

Step Angle (degrees): 1.8°

Phase Resistance: ~2.8Ω/Phase

Test Conditions:

◾ A4988 driver used for all tests

◾ Tested at 25%, 50%, 75%, and 100% of the rated current

◾ Tested with a driver supply voltage of 12V and 24V

*(some of the higher-voltage, higher-current data points were corrupted due to driver overload)

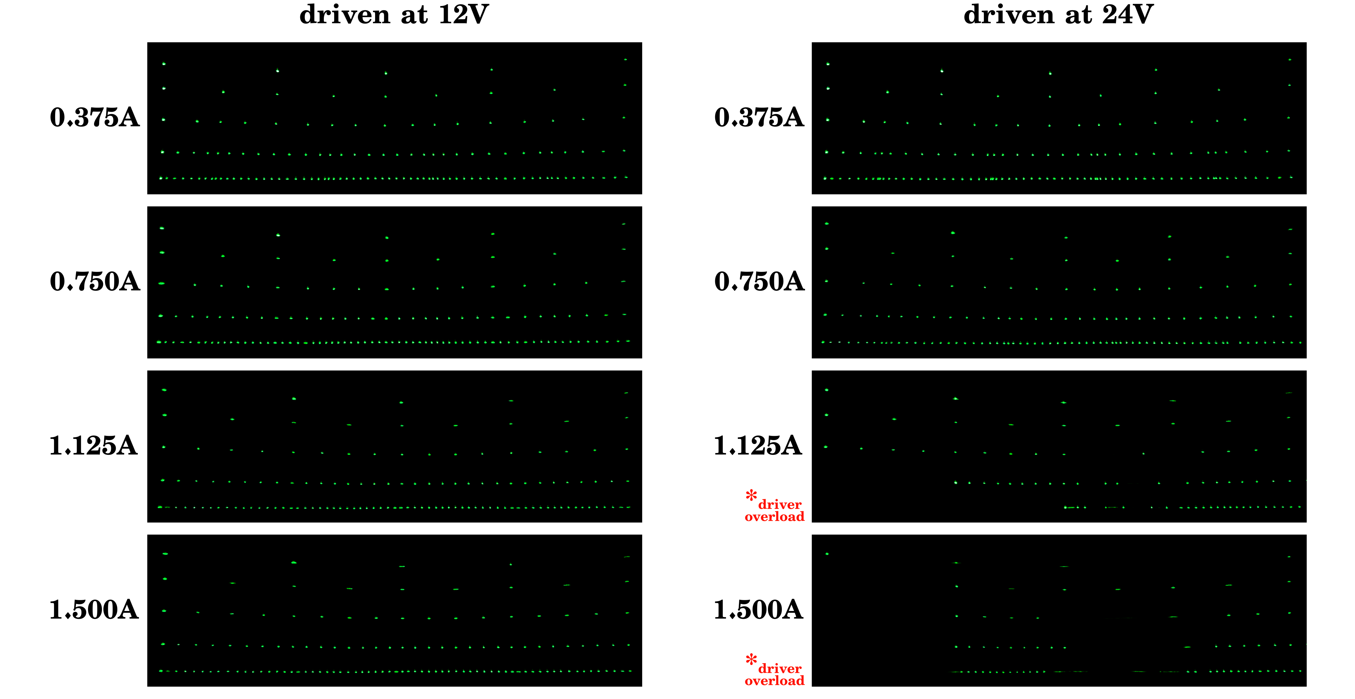
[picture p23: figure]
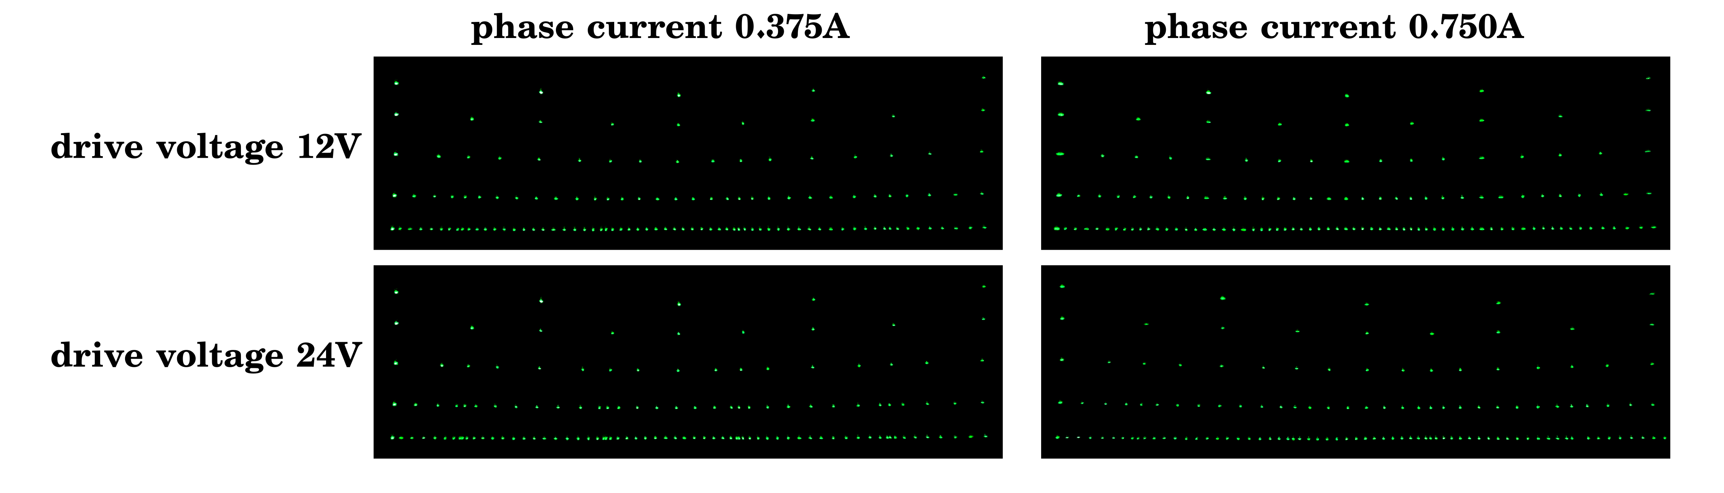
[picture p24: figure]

Notes:

◾ Every pattern was created at the indicated voltage and current levels by a laser galvo projector with the X-mirror actuated by the test subject. In automated fashion, a line of dots was drawn with the driver set to full steps, then the same row in half steps lined up underneath, then quarter steps, etc., all the way down to sixteenth steps.

◾ Due to the limited exposure duration of my camera, some combinations of drive current and voltage resulted in motion blur from the mirror ‘bouncing’ more than usual before settling at its intended target position. Other than in extreme cases, this should not significantly impact data accuracy.

◾ At ‘high’ voltages and currents of 24 volts and more than 1 ampere, the A4988 driver quickly overheats, which seems to make it extremely susceptible to electrical noise and glitching and unfortunately resulted in erratic behavior like lost steps, making execution of a complete test pattern impossible. Step detent points should still be valid wherever they visually appear in the correct location though.

KYSAN 1124090 / 42BYGH4803

Chronic Mechatronic stepper motor benchmark – Creative Commons BY-SA 4.0 (https://creativecommons.org/licenses/by-sa/4.0/)

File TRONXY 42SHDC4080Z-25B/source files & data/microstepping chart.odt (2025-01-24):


Microstepping Chart

Frame Size: NEMA 17

Rated Current: DC 1.8A/Phase (assumed value)

Holding Torque: ~0.55N·m (assumed value)

Step Angle (degrees): 1.8°

Phase Resistance: ~1.6Ω/Phase

Test Conditions:

◾ A4988 driver used for all tests

◾ Tested at 25%, 50%, 75%, and 100% of the rated current

◾ Tested with a driver supply voltage of 12V and 24V

*(some of the higher-voltage, higher-current data points were corrupted due to driver overload)


Notes:

◾ Every pattern was created at the indicated voltage and current levels by a laser galvo projector with the X-mirror actuated by the test subject. In automated fashion, a line of dots was drawn with the driver set to full steps, then the same row in half steps lined up underneath, then quarter steps, etc., all the way down to sixteenth steps.

◾ Due to the limited exposure duration of my camera, some combinations of drive current and voltage resulted in motion blur from the mirror ‘bouncing’ more than usual before settling at its intended target position. Other than in extreme cases, this should not significantly impact data accuracy.

◾ At ‘high’ voltages and currents of 24 volts and more than 1 ampere, the A4988 driver quickly overheats, which seems to make it extremely susceptible to electrical noise and glitching and unfortunately resulted in erratic behavior like lost steps, making execution of a complete test pattern impossible. Step detent points should still be valid wherever they visually appear in the correct location though.

TRONXY 42SHDC4080Z

Chronic Mechatronic stepper motor benchmark – Creative Commons BY-SA 4.0 (https://creativecommons.org/licenses/by-sa/4.0/)

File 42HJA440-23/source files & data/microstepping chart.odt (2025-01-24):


Microstepping Chart

Frame Size: NEMA 17

Rated Current: DC 1.64A/Phase (assumed value)

Holding Torque: ~0.43N·m (assumed value)

Step Angle (degrees): 1.8°

Phase Resistance: ~1.5Ω/Phase

Test Conditions:

◾ A4988 driver used for all tests

◾ Tested at 25%, 50%, 75%, and 100% of the rated current

◾ Tested with a driver supply voltage of 12V and 24V

*(some of the higher-voltage, higher-current data points were corrupted due to driver overload)


Notes:

◾ Every pattern was created at the indicated voltage and current levels by a laser galvo projector with the X-mirror actuated by the test subject. In automated fashion, a line of dots was drawn with the driver set to full steps, then the same row in half steps lined up underneath, then quarter steps, etc., all the way down to sixteenth steps.

◾ Due to the limited exposure duration of my camera, some combinations of drive current and voltage resulted in motion blur from the mirror ‘bouncing’ more than usual before settling at its intended target position. Other than in extreme cases, this should not significantly impact data accuracy.

◾ At ‘high’ voltages and currents of 24 volts and more than 1 ampere, the A4988 driver quickly overheats, which seems to make it extremely susceptible to electrical noise and glitching and unfortunately resulted in erratic behavior like lost steps, making execution of a complete test pattern impossible. Step detent points should still be valid wherever they visually appear in the correct location though.

GENERIC 42HJA440

Chronic Mechatronic stepper motor benchmark – Creative Commons BY-SA 4.0 (https://creativecommons.org/licenses/by-sa/4.0/)

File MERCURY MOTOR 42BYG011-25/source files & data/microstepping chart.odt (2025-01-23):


Microstepping Chart

Frame Size: NEMA 17

Rated Current: DC 0.33A/Phase

Holding Torque: 0.23N·m

Step Angle (degrees): 1.8°

Phase Resistance: ~34Ω/Phase

Test Conditions:

◾ A4988 driver used for all tests

◾ Tested at 25%, 50%, 75%, and 100% of the rated current

◾ Tested with a driver supply voltage of 12V and 24V


Notes:

◾ Every pattern was created at the indicated voltage and current levels by a laser galvo projector with the X-mirror actuated by the test subject. In automated fashion, a line of dots was drawn with the driver set to full steps, then the same row in half steps lined up underneath, then quarter steps, etc., all the way down to sixteenth steps.

◾ Due to the limited exposure duration of my camera, some combinations of drive current and voltage resulted in motion blur from the mirror ‘bouncing’ more than usual before settling at its intended target position. Other than in extreme cases, this should not significantly impact data accuracy.

MERCURY MOTOR SM-42BYG011

Chronic Mechatronic stepper motor benchmark – Creative Commons BY-SA 4.0 (https://creativecommons.org/licenses/by-sa/4.0/)

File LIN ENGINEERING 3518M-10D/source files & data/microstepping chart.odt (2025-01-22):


Microstepping Chart

Frame Size: NEMA 14

Rated Current: DC 1.5A/Phase

Holding Torque: (unknown)

Step Angle (degrees): 1.8°

Phase Resistance: ~1.0Ω/Phase

Test Conditions:

◾ A4988 driver used for all tests

◾ Tested at 25%, 50%, 75%, and 100% of the rated current

◾ Tested with a driver supply voltage of 12V and 24V

*(some of the higher-voltage, higher-current data points were corrupted due to driver overload)


Notes:

◾ Every pattern was created at the indicated voltage and current levels by a laser galvo projector with the X-mirror actuated by the test subject. In automated fashion, a line of dots was drawn with the driver set to full steps, then the same row in half steps lined up underneath, then quarter steps, etc., all the way down to sixteenth steps.

◾ Due to the limited exposure duration of my camera, some combinations of drive current and voltage resulted in motion blur from the mirror ‘bouncing’ more than usual before settling at its intended target position. Other than in extreme cases, this should not significantly impact data accuracy.

◾ At ‘high’ voltages and currents of 24 volts and more than 1 ampere, the A4988 driver quickly overheats, which seems to make it extremely susceptible to electrical noise and glitching and unfortunately resulted in erratic behavior like lost steps, making execution of a complete test pattern impossible. Step detent points should still be valid wherever they visually appear in the correct location though.

LIN ENGINEERING 3518M

Chronic Mechatronic stepper motor benchmark – Creative Commons BY-SA 4.0 (https://creativecommons.org/licenses/by-sa/4.0/)

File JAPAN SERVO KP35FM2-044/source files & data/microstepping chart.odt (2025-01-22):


Microstepping Chart

Frame Size: NEMA 14

Rated Current: DC 0.5A/Phase

Holding Torque: 0.069N·m

Step Angle (degrees): 1.8°

Phase Resistance: ~8Ω/Phase

Test Conditions:

◾ A4988 driver used for all tests

◾ Tested at 25%, 50%, 75%, and 100% of the rated current

◾ Tested with a driver supply voltage of 12V and 24V


Notes:

◾ Every pattern was created at the indicated voltage and current levels by a laser galvo projector with the X-mirror actuated by the test subject. In automated fashion, a line of dots was drawn with the driver set to full steps, then the same row in half steps lined up underneath, then quarter steps, etc., all the way down to sixteenth steps.

◾ Due to the limited exposure duration of my camera, some combinations of drive current and voltage resulted in motion blur from the mirror ‘bouncing’ more than usual before settling at its intended target position. Other than in extreme cases, this should not significantly impact data accuracy.

JAPAN SERVO KP35FM2

Chronic Mechatronic stepper motor benchmark – Creative Commons BY-SA 4.0 (https://creativecommons.org/licenses/by-sa/4.0/)

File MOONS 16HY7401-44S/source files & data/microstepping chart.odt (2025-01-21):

Microstepping Chart


Frame Size: NEMA 16

Rated Current: DC 0.4A/Phase

Holding Torque: 0.064N·m

Step Angle (degrees): 1.8°

Phase Resistance: ~6.6Ω/Phase

Test Conditions:

◾ A4988 driver used for all tests

◾ Tested at 25%, 50%, 75%, and 100% of the rated current

◾ Tested with a driver supply voltage of 12V and 24V


Notes:

◾ Every pattern was created at the indicated voltage and current levels by a laser galvo projector with the X-mirror actuated by the test subject. In automated fashion, a line of dots was drawn with the driver set to full steps, then the same row in half steps lined up underneath, then quarter steps, etc., all the way down to sixteenth steps.

◾ Due to the limited exposure duration of my camera, some combinations of drive current and voltage resulted in motion blur from the mirror ‘bouncing’ more than usual before settling at its intended target position. Other than in extreme cases, this should not significantly impact data accuracy.

Chronic Mechatronic stepper motor benchmark – Creative Commons BY-SA 4.0 (https://creativecommons.org/licenses/by-sa/4.0/)

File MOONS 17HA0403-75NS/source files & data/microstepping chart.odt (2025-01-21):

Microstepping Chart


Frame Size: NEMA 17

Rated Current: DC 0.43A/Phase

Holding Torque: 0.09N·m

Step Angle (degrees): 0.9°

Phase Resistance: ~8Ω/Phase

Test Conditions:

◾ A4988 driver used for all tests

◾ Tested at 25%, 50%, 75%, and 100% of the rated current

◾ Tested with a driver supply voltage of 12V and 24V


Notes:

◾ Every pattern was created at the indicated voltage and current levels by a laser galvo projector with the X-mirror actuated by the test subject. In automated fashion, a line of dots was drawn with the driver set to full steps, then the same row in half steps lined up underneath, then quarter steps, etc., all the way down to sixteenth steps.

◾ Due to the limited exposure duration of my camera, some combinations of drive current and voltage resulted in motion blur from the mirror ‘bouncing’ more than usual before settling at its intended target position. Other than in extreme cases, this should not significantly impact data accuracy.

◾ For convenient presentation of the data, all images on this chart were slightly scaled down vertically to achieve a wider aspect ratio. This does make all dots slightly oval-shaped but shouldn’t invalidate the data in any way.

Chronic Mechatronic stepper motor benchmark – Creative Commons BY-SA 4.0 (https://creativecommons.org/licenses/by-sa/4.0/)

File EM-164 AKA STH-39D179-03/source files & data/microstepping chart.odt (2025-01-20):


Microstepping Chart

Frame Size: NEMA 16

Rated Current: DC 0.74A/Phase

Holding Torque: (unknown)

Step Angle (degrees): 1.8°

Phase Resistance: ~2.9Ω/Phase *

Test Conditions:

◾ A4988 driver used for all tests

◾ Tested at 25%, 50%, 75%, and 100% of the rated current

◾ Tested with a driver supply voltage of 12V and 24V


Notes:

◾ Every pattern was created at the indicated voltage and current levels by a laser galvo projector with the X-mirror actuated by the test subject. In automated fashion, a line of dots was drawn with the driver set to full steps, then the same row in half steps lined up underneath, then quarter steps, etc., all the way down to sixteenth steps.

◾ Due to the limited exposure duration of my camera, some combinations of drive current and voltage resulted in motion blur from the mirror ‘bouncing’ more than usual before settling at its intended target position. Other than in extreme cases, this should not significantly impact data accuracy.

◾ * This stepper motor was originally unipolar with a phase resistance of about 5.9 ohms, but I reconfigured the windings for a bipolar arrangement. I decided to wire both halves of the coils (left and right of the center tap, figuratively speaking) in parallel to reduce inductance for faster maximum speeds.

Chronic Mechatronic stepper motor benchmark – Creative Commons BY-SA 4.0 (https://creativecommons.org/licenses/by-sa/4.0/)

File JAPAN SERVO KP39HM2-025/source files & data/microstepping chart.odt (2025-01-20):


Microstepping Chart

Frame Size: NEMA 16

Rated Current: DC 0.23A/Phase

Holding Torque: (unknown)

Step Angle (degrees): 1.8°

Phase Resistance: ~36.4Ω/Phase *

Test Conditions:

◾ A4988 driver used for all tests

◾ Tested at 25%, 50%, 75%, and 100% of the rated current

◾ Tested with a driver supply voltage of 12V and 24V


Notes:

◾ Every pattern was created at the indicated voltage and current levels by a laser galvo projector with the X-mirror actuated by the test subject. In automated fashion, a line of dots was drawn with the driver set to full steps, then the same row in half steps lined up underneath, then quarter steps, etc., all the way down to sixteenth steps.

◾ Due to the limited exposure duration of my camera, some combinations of drive current and voltage resulted in motion blur from the mirror ‘bouncing’ more than usual before settling at its intended target position. Other than in extreme cases, this should not significantly impact data accuracy.

◾ * This stepper motor was originally unipolar with a phase resistance of about 74 ohms, but I reconfigured the windings for a bipolar arrangement. I decided to wire both halves of the coils (left and right of the center tap, figuratively speaking) in parallel to reduce inductance for faster maximum speeds.

JAPAN SERVO KP39HM2

Chronic Mechatronic stepper motor benchmark – Creative Commons BY-SA 4.0 (https://creativecommons.org/licenses/by-sa/4.0/)

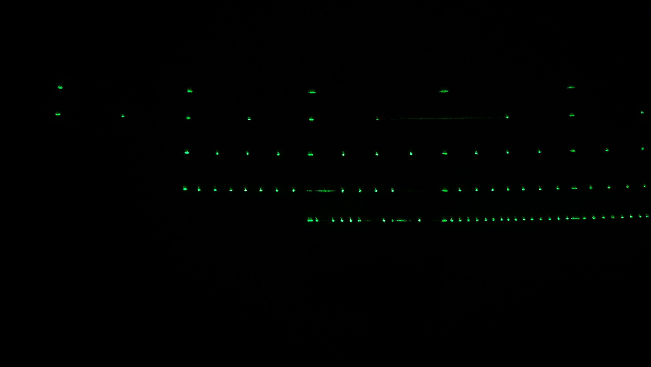
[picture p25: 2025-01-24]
HANPOSE 17HS4401/source files & data/IMG_20241223_013024 HANPOSE 17HS4401 24V_1.5A.jpg

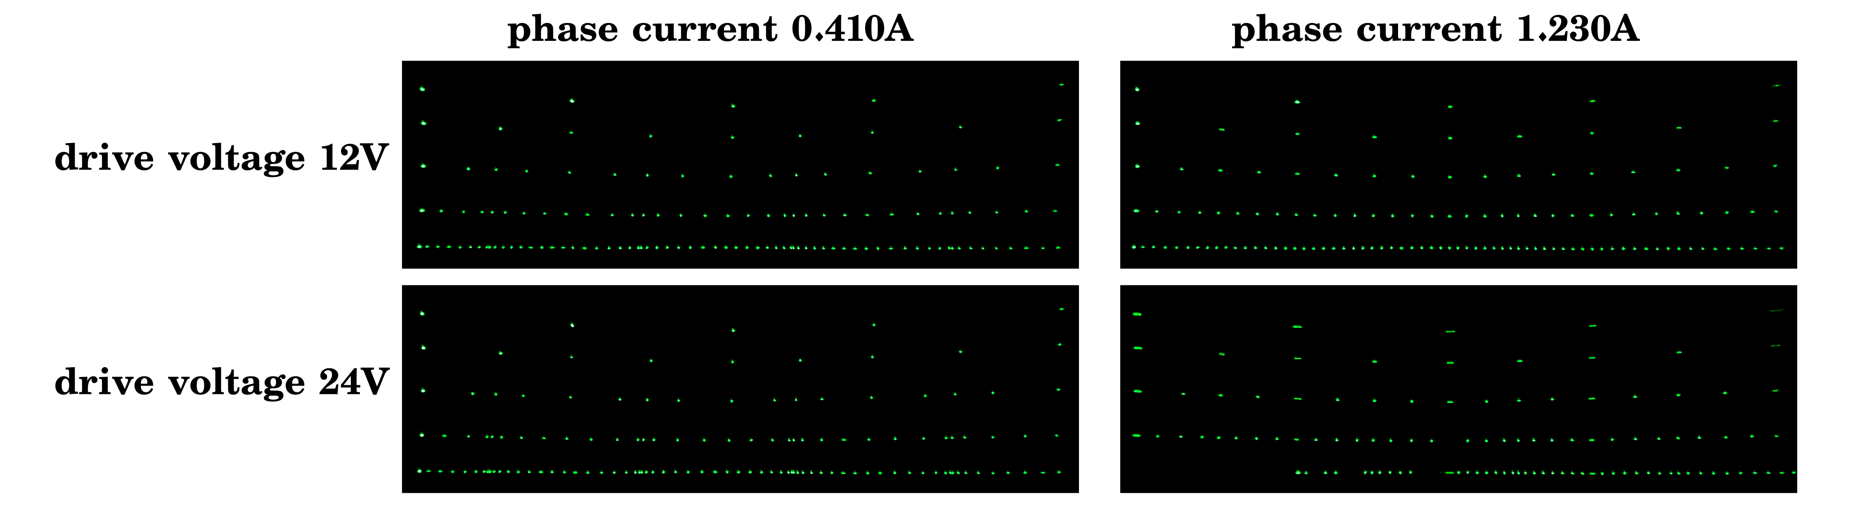
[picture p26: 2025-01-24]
42HJA440-23/voltage comparison chart.png

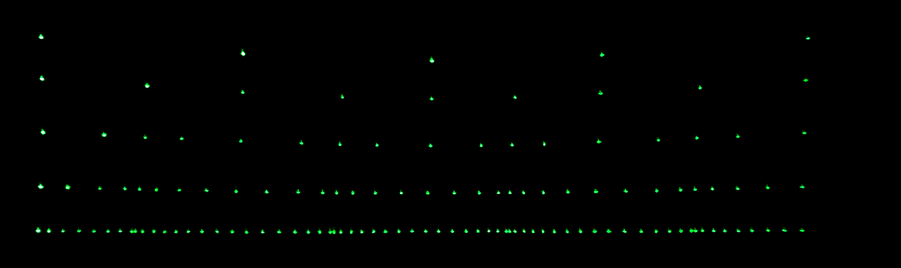
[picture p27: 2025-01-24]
TRONXY 42SHDC4080Z-25B/source files & data/TRONXY 42SHDC4080Z 12V_0.45A.png

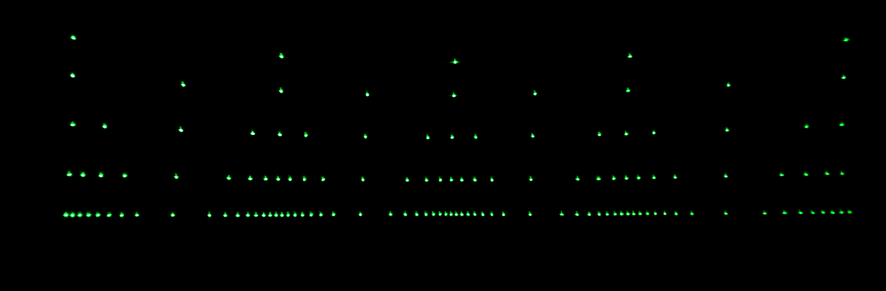
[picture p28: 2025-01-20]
JAPAN SERVO KP39HM2-025/source files & data/JAPAN SERVO KP39HM2 24V_0.23A.png

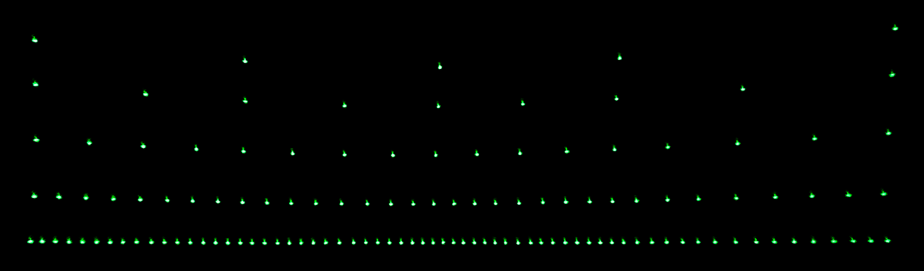
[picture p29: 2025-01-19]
EPSON EM-258/source files & data/EPSON EM-258 12V_0.525A.png

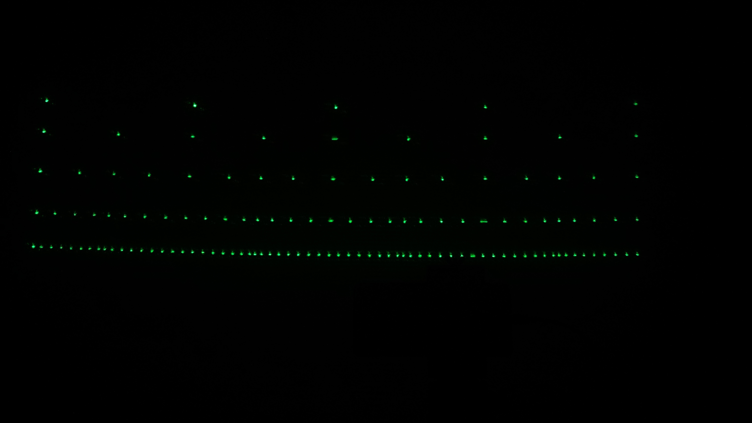
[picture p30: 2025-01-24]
WANTAI MOTOR 42BYGHW609-1/source files & data/IMG_20241223_014858 WANTAI STEPPER 42BYGHW609 12V_0.85A.jpg

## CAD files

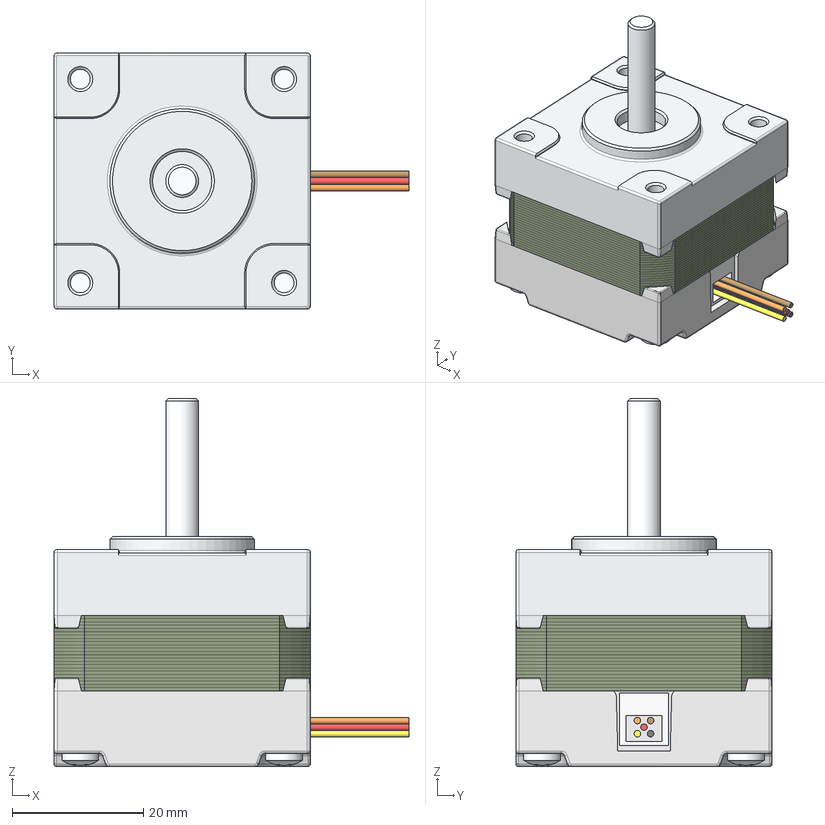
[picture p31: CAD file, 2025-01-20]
JAPAN SERVO KP39HM2-025/KP39HM2-025 Japan Servo CO LTD.step
54.0 x 39.0 x 56.0 mm
front endcap
stator
rear endcap
shaft
wire grommet
black wire
red wire
yellow wire
orange wire
brown wire
M3x27-Screw x 4

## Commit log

2025-01-19 Update description.md
    Add CAD model link
2025-01-22 Rename 3518M-07 _ Hybrid Stepper Motor _ Lin Engineering.pdf to 3518M_series_ Hybrid Stepper Motor_specifications _ Lin Engineering.pdf
